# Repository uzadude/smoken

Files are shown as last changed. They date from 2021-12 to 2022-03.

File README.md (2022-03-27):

# Smoken!
A temperature controlled fan for charcoal smoker using ESP32.
 
## Background
After taking a welding course, I decided to build a smoker. Shortly after, I realized I must have a solution to keep the temperature steady for many hours. Searching around the internet I found only terribly expensive products (like the [FIREBOARD](https://www.fireboard.com/shop/fireboard-2-drive/?fba_ref=14)). That motivated me to try my first IOT project!

I took this opportunity to gain some skills in the electrical engineering domain.
I used an ESP32 for the MCU (started from [ESP32 starter kit](https://www.ebay.com/itm/303652581313)), built a working prototype using a breadboard and then went on to design a PCB for it (using [KiCad](https://www.kicad.org/)).

I will try to highlight the main lessons learned throughout this process.

## How It Works
- An ESP32 is connected to a thermocouple (with max6675 amplifier) to measure the smoker's current temprature. Another thermocouple is connected just to monitor the meat's temprature.
- The ESP32 is also connected to a 4-pin fan and controls it through a PWM channel with A PID algorithm.
- An external power of 12V/5A is used for both the fan and the ESP32 (through a step-down regulator).
- An 1602 LCD screen is used for simple information.
- A web server is used to monitor the current status, and configure things like the wifi credentials and some paramteres.
- A potentiometer is also available to have manual control over the fan.

### Circuit Schema
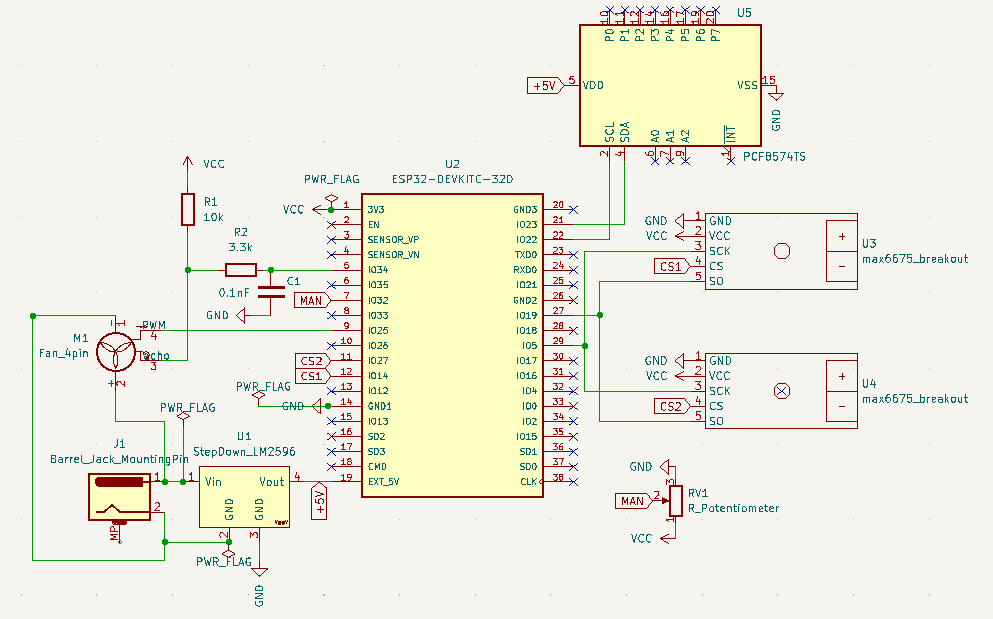
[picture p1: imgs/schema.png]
Smoker Fan Schema


### Inventory List

|name|price|quantity|
|----|----|---|
|Esp 32|4|1
|12v power supply|3.7|1
|12v/3A blower fan 4pin|15.4|1
|12v to 5v step down|4|4
|LCD 1602|2.4|1
|max6675|7.3|2
|thermocouple|5.3|2
|small bread board|4.3|3
|4p connector|2.6|10
|wire 4p|5|5m
|3.3k resistor|1.5|300
|wires|3|120

### Afterthoughts
- I could have used a much weaker fan
- Replace the 1602 LCD with 12864 OLED

### Gotchas
- Fan's tacho required RC filter to get the correct reading
- Pin 4 as ADC with wifi.h [bug](https://github.com/espressif/arduino-esp32/issues/102)

## Code
- Use Platform IO as it is way more convenient than the Arduino IDE
- Web server using ESPAsyncWebServer
- Web-based config using AsyncWebConfig
- Use the SPIFFS to save data like a webpage, config file, and data history
- Use git from the beginning

### Gotchas
- [PWM's max freq/precision](src/fan.cpp#L18)

### Some Refs
- basic ESP32 examples:
  - https://lastminuteengineers.com/handling-esp32-gpio-interrupts-tutorial/

- connect max6675:
  - https://github.com/adafruit/MAX6675-library/blob/master/examples/serialthermocouple/serialthermocouple.ino
  - http://www.esp32learning.com/code/esp32-and-max6675-example.php

- connect multiple max6675:
  - https://arduino.stackexchange.com/questions/37193/multiple-3-wire-spi-sensor-interfacing-with-arduino
  - https://forum.arduino.cc/t/problem-with-multiple-max6675-thermocouple/573336/7

- Circuit example:
  - https://github.com/KlausMu/esp32-fan-controller

- PID:
  - https://playground.arduino.cc/Code/PIDLibrary/

- Another ref project:
  - https://github.com/chris948/esp_grillcon/blob/master/esp_grillcon.ino

- Fan specs:
  - https://www.mouser.co.il/datasheet/2/632/BFB1012EH-C18J-1602075.pdf

## PCB

- Used KiCAD
- YouTube tutorial:
  - https://www.youtube.com/watch?v=vaCVh2SAZY4
- Nice getting started tutorial:
  - https://medium.com/invent-io/getting-started-with-embedded-systems-3-schematic-pcb-design-manufacturing-5566b2cf6963
- To search and download additional CAD modules:
  - https://www.snapeda.com/home/
  - https://grabcad.com/library
- Ordered PCB from:
  - https://jlcpcb.com/

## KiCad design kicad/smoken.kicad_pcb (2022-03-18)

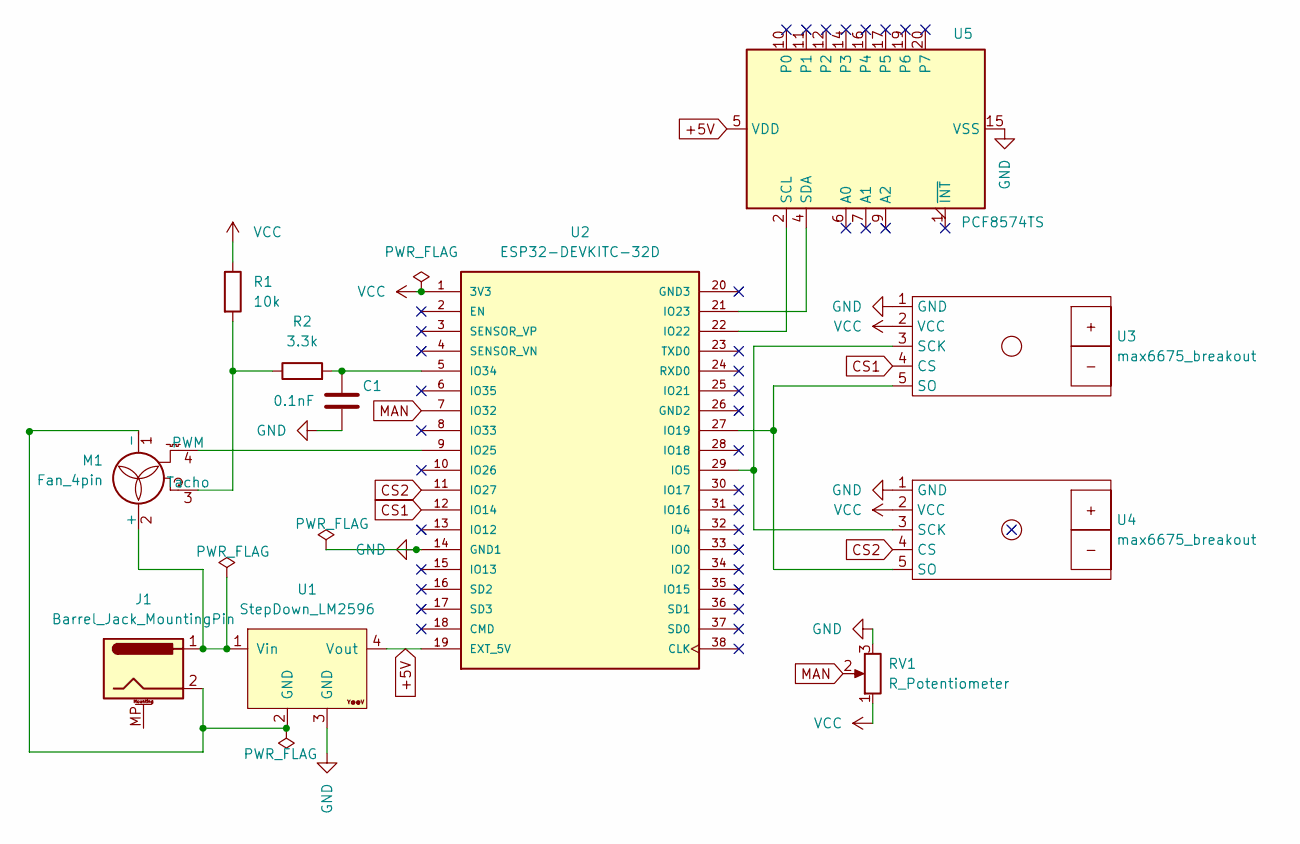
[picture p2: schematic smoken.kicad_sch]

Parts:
C1: 0.1nF; CP_Radial_D4.0mm_P2.00mm
J1: Barrel_Jack_MountingPin; BarrelJack_GCT_DCJ200-10-A_Horizontal
M1: Fan_4pin; PinHeader_1x04_P2.54mm_Vertical
R1: 10k; R_Axial_DIN0204_L3.6mm_D1.6mm_P5.08mm_Horizontal
R2: 3.3k; R_Axial_DIN0204_L3.6mm_D1.6mm_P5.08mm_Horizontal
RV1: R_Potentiometer; Potentiometer_Omeg_PC16BU_Vertical
U1: StepDown_LM2596; YAAJ_DCDC_StepDown_LM2596
U2: ESP32-DEVKITC-32D; MODULE_ESP32-DEVKITC-32D; PARTREV 4
U3, U4: max6675_breakout
U5: PCF8574TS; lcd1602_breakout

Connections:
+5V: U1.4 (Vout), U2.19 (EXT_5V), U5.5 (VDD)
CS1: U2.12 (IO14), U3.4 (CS)
CS2: U2.11 (IO27), U4.4 (CS)
GND: C1.2, RV1.3, U1.3 (GND), U2.14 (GND1), U3.1 (GND), U4.1 (GND), U5.15 (VSS)
MAN: RV1.2, U2.7 (IO32)
unnamed: J1.2, M1.1 (-), U1.2 (GND)
unnamed: J1.1, M1.2 (+), U1.1 (Vin)
unnamed: M1.3 (Tacho), R1.2, R2.1
unnamed: C1.1, R2.2, U2.5 (IO34)
unnamed: M1.4 (PWM), U2.9 (IO25)
unnamed: U2.21 (IO23), U5.4 (SDA)
unnamed: U2.22 (IO22), U5.2 (SCL)
unnamed: U2.27 (IO19), U3.5 (SO), U4.5 (SO)
unnamed: U2.29 (IO5), U3.3 (SCK), U4.3 (SCK)
VCC: R1.1, RV1.1, U2.1 (3V3), U3.2 (VCC), U4.2 (VCC)

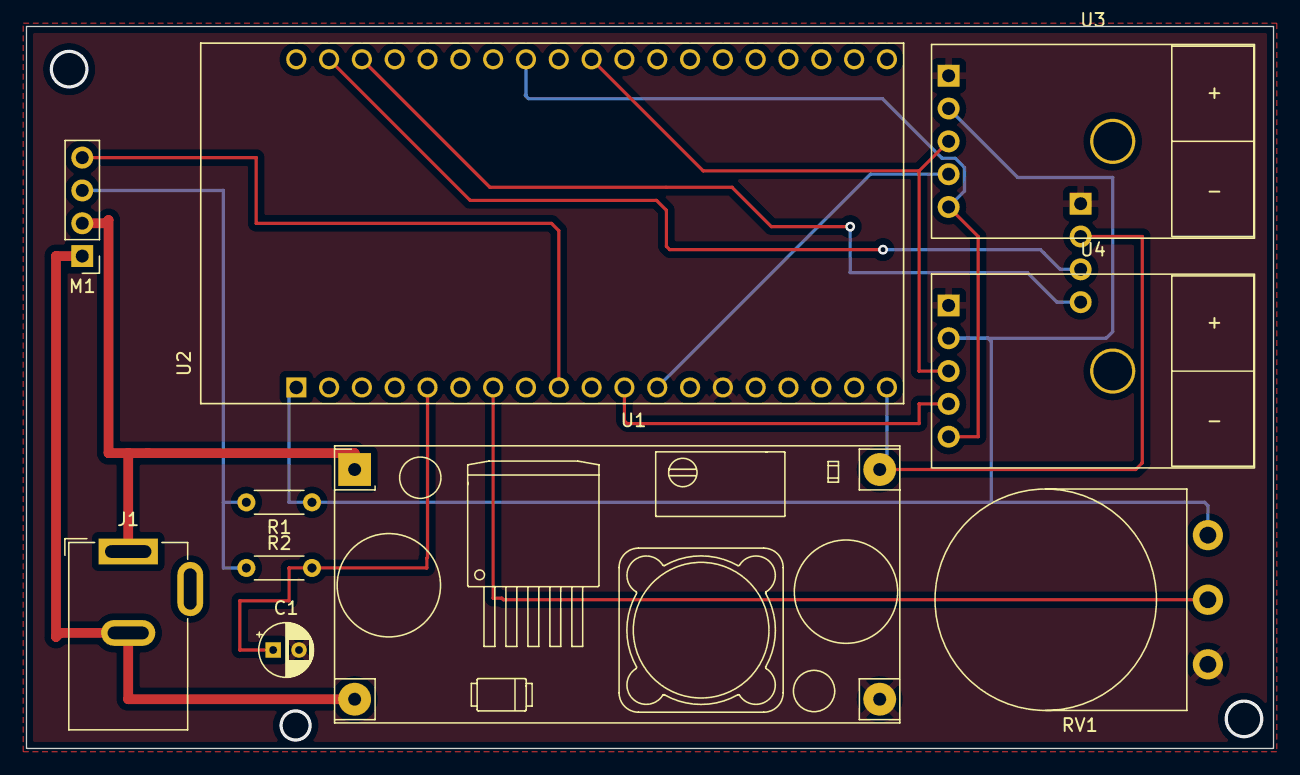
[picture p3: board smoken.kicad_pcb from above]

Board: 2 copper layers, 96.5 x 55.9 mm, 11 parts (1 on the bottom side), 15 nets.

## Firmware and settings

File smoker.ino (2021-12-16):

#include <Wire.h>
#include <LiquidCrystal_I2C.h>
#include <max6675.h>
#include <PID_v1.h>
#include <WiFi.h>
#include <WebServer.h>


// wifi
/// AP
//const char* ssid = "smoken";
//const char* password = "12345678";
//IPAddress local_ip(192,168,1,1);
//IPAddress gateway(192,168,1,1);
//IPAddress subnet(255,255,255,0);

/// Station
const char* ssid = "***REMOVED***";
const char* password = "***REMOVED***";

// Web Server
WebServer server(80);

// PID
double Setpoint, Input, Output;
PID myPID(&Input, &Output, &Setpoint, 2, 5, 1, DIRECT);

// thermocouple
int thermoSO = 19;
int thermoSCK = 5;
int thermoCS1 = 23;
int thermoCS2 = 22;

MAX6675 tc1(thermoSCK, thermoCS1, thermoSO);
MAX6675 tc2(thermoSCK, thermoCS2, thermoSO);


// LCD
#define SDA 13                    //Define SDA pins
#define SCL 14                    //Define SCL pins
LiquidCrystal_I2C lcd(0x27,16,2); //initialize the LCD
#define NUM_SCREENS 2
char lcdBuffer[NUM_SCREENS][2][16];
int curScreen = 0;
unsigned long lcdMillis;

// fan
#define PIN_POTEN    32 // (4) doesn't work with wifi.h
#define PIN_FAN_PWM 25
#define CHAN_PWM     0

// tacho defs
#define PIN_FAN_TACHO 34
#define RPM_CALC_PERIOD 1000
int fan1RPM = 0;
volatile int fan1InterruptCounter;
unsigned long previousmills;

void IRAM_ATTR handleInterruptFan1Tacho()
{
  fan1InterruptCounter++;
}

void printLCD() {

  if (millis() - lcdMillis > 3000) {
   lcdMillis = millis();
   curScreen++;
   curScreen = curScreen % NUM_SCREENS;
  }
  
  lcd.setCursor(0, 0);              
  lcd.printf("%-16s", lcdBuffer[curScreen][0]);
  lcd.setCursor(0, 1);              
  lcd.printf("%-16s", lcdBuffer[curScreen][1]);

  Serial.println(lcdBuffer[curScreen][0]);
  Serial.println(lcdBuffer[curScreen][1]);
  
}


void setup()
{
  Serial.begin(9600);
  Serial.println("starting..");

  // Thermocouples init
  digitalWrite(thermoCS1, LOW);
  digitalWrite(thermoCS2, LOW);

  // Fan
  
  /// PWM
  // Our fan requests freq=25Khz. ESP32's spec for precision bound us to max of 11bits.
  // (max frequency is 80M/11^2=39K)
  ledcSetup(CHAN_PWM, 25000, 8); 
  ledcAttachPin(PIN_FAN_PWM, CHAN_PWM);

  // tacho
  pinMode(PIN_FAN_TACHO, INPUT_PULLUP);
  attachInterrupt(PIN_FAN_TACHO, handleInterruptFan1Tacho, FALLING);
  previousmills = millis();

  // LCD init
  Wire.begin(SDA, SCL);
  lcd.init();
  lcd.backlight();
  lcdMillis = millis();

  Setpoint = 30;
  myPID.SetOutputLimits(0, 255);
  myPID.SetMode(AUTOMATIC);

  // Wifi
  //WiFi.softAP(ssid, password);
  //WiFi.softAPConfig(local_ip, gateway, subnet);
  //delay(100);

  WiFi.begin(ssid, password);

  //check wi-fi is connected to wi-fi network
  while (WiFi.status() != WL_CONNECTED) {
    delay(1000);
    Serial.print(".");
  }
  Serial.println("");
  Serial.println("WiFi connected..!");
  Serial.print("Got IP: ");
  Serial.println(WiFi.localIP());

  // Web Server
  server.on("/", handle_OnConnect);
  //server.on("/led1on", handle_led1on);
  server.onNotFound(handle_NotFound);
  
  server.begin();
  Serial.println("HTTP server started");
  
  delay(300);
}
 
void loop()
{

  server.handleClient();

  digitalWrite(thermoCS1, LOW);
  Input = tc1.readCelsius();
  digitalWrite(thermoCS1, HIGH);
  myPID.Compute();

  delay(100);
  digitalWrite(thermoCS2, LOW);
  double tmp2 = tc2.readCelsius();
  digitalWrite(thermoCS2, HIGH);
  delay(100);
 
  sprintf(lcdBuffer[0][0], "%3.0f %3.0f %3.0f", Input, tmp2, Setpoint);
   
  int adcVal = analogRead(PIN_POTEN); //read adc (12 bit)
  Serial.printf("ADC Val: %d\n", adcVal);

  sprintf(lcdBuffer[0][1], "Man:%3.0f Aut:%3.0f", adcVal/4095.0*100, Output/255*100);

  int pwmVal=0;
  // set fan's PWM manually if adc>0, otherwise by PID
  if (adcVal>0) {
    pwmVal = map(adcVal, 0, 4095, 0, 255);  // re-map to pwmVal (8 bit)
  } else {
    pwmVal = (int) Output;
  }

  double pwmPct = pwmVal / 255.0 * 100;
  
  Serial.printf("PWM: %d, \t pct: %.2f\n", pwmVal, pwmPct);
  sprintf(lcdBuffer[1][0], "PWM pct: %3.0f%%", pwmPct);

  // set the PWM duty. fan specs states that min val is 30%.
  if (pwmPct>30) {
    ledcWrite(CHAN_PWM, pwmVal);
  } else {
   ledcWrite(CHAN_PWM, 0); 
  }

  // calc fan RPM
  if (millis() - previousmills > RPM_CALC_PERIOD) {
    int elapsedMs = millis() - previousmills;
    int count = fan1InterruptCounter;
    fan1InterruptCounter = 0;
    previousmills = millis();

    fan1RPM = (int) (count * 60.0 / 2 * 1000 / elapsedMs);
    Serial.println(fan1RPM);

    sprintf(lcdBuffer[1][1], "RPM: %8d", fan1RPM);
    //sprintf(buffer, "c: %8d", count);
  }

  printLCD();
 
  delay(1000);
}

void handle_OnConnect() {
  server.send(200, "text/html", SendHTML()); 
}

void handle_NotFound(){
  server.send(404, "text/plain", "Not found");
}

String SendHTML(){
  String ptr = "<!DOCTYPE html> <html>\n";
  ptr +="<head><meta name=\"viewport\" content=\"width=device-width, initial-scale=1.0, user-scalable=no\">\n";
  ptr +="<title>Smoken PID control</title>\n";
  ptr +="<style>html { font-family: Helvetica; display: inline-block; margin: 0px auto; text-align: center;}\n";
  ptr +="body{margin-top: 50px;} h1 {color: #444444;margin: 50px auto 30px;} h3 {color: #444444;margin-bottom: 50px;}\n";
  ptr +=".button {display: block;width: 80px;background-color: #3498db;border: none;color: white;padding: 13px 30px;text-decoration: none;font-size: 25px;margin: 0px auto 35px;cursor: pointer;border-radius: 4px;}\n";
  ptr +=".button-on {background-color: #3498db;}\n";
  ptr +=".button-on:active {background-color: #2980b9;}\n";
  ptr +=".button-off {background-color: #34495e;}\n";
  ptr +=".button-off:active {background-color: #2c3e50;}\n";
  ptr +="p {font-size: 14px;color: #888;margin-bottom: 10px;}\n";
  ptr +="</style>\n";
  ptr +="</head>\n";
  ptr +="<body>\n";
  ptr +="<h1>Smoken Web Server</h1>\n";

  //ptr +="<p>LED2 Status: ON</p><a class=\"button button-off\" href=\"/led2off\">OFF</a>\n";
  ptr +="<a class=\"button button-off\" href=\"/led2off\">Update</a>\n";

  ptr +="</body>\n";
  ptr +="</html>\n";
  return ptr;
}

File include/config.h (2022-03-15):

// --- thermocouple -----------------------------------------------------------------------------------------------------------------------

const int thermoSO = 19;
const int thermoSCK = 5;
const int thermoCS1 = 14;
const int thermoCS2 = 27;


// --- fan --------------------------------------------------------------------------------------------------------------------------------

// potentionmeter
#define PIN_POTEN    32 // (4) doesn't work with wifi.h
#define PIN_FAN_PWM  25
#define CHAN_PWM     0

// tacho defs
#define PIN_FAN_TACHO 34
#define RPM_CALC_PERIOD 1000


// --- LCD --------------------------------------------------------------------------------------------------------------------------------
// SDA/SCL must be connected to 21/22
#define NUM_SCREENS 2

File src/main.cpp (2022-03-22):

#include <config.h>
#include <Wire.h>
#include <HardwareSerial.h>
#include <thermocouple.h>
#include <fan.h>
#include <lcd.h>
#include <pid.h>
#include <wifi.h>
#include <web_server.h>
#include <web_config.h>
#include <pwm.h>
#include <data.h>

void setup()
{
  Serial.begin(9600);
  Serial.println("starting..");

  initFan();
  initData();
  initLCD();

  initConfig();
  initWIFI();
  initWebServer();

  initThermocouple();

  setPIDconfs(conf.getInt("setpoint"), conf.getInt("fmin"), conf.getInt("fmax"),
              conf.getFloat("kp"), conf.getFloat("ki"), conf.getFloat("kd"));
  //setPIDconfs(30, 0, 255, 2, 5, 1);

  delay(2000);
}
 
void loop()
{

  //server.handleClient();

  double tmp1 = readTC(0);
  updatePID(tmp1);

  double tmp2 = readTC(1);
  sprintf(getLCDbuffer(0,0), "%3.0f %3.0f %3d", tmp1, tmp2, conf.getInt("setpoint"));

  handlePWM();

  int fan_rpm = getFanRPM();
  sprintf(getLCDbuffer(1, 1), "RPM: %8d", fan_rpm);

  addReads(tmp1, tmp2, (double) conf.getInt("setpoint"), getPWM(), fan_rpm);

  refreshLCD();
 
  delay(1000);
}

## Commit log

2021-12-09 working potentiometer with PWM
2021-12-09 added Tacho and fixed PWM wrong precision
    [smoker.ino]
2021-12-09 adding PID
2021-12-12 fixing ADC and wifi bug
    [smoker.ino]
2021-12-16 extracting also PWM
2022-03-15 change thermo CS pin
2022-03-18 PCB - kicad files
    [smoken.kicad_pcb, smoken.kicad_sch]
2022-03-22 changing PID params from int to float
2022-03-22 setting PWM to zero on start to prevent fan from start spinning
    [fan.cpp, main.cpp]
